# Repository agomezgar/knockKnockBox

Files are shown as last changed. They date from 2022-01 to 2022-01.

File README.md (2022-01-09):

# Knockknockbox Español

Un rediseño (un homenaje, si lo prefieres) de la mítica #KnockKnockBox con la que hemos jugado en tantos centros educativos gracias a los talleres Verkstadt de David Cuartielles
<p align="center">
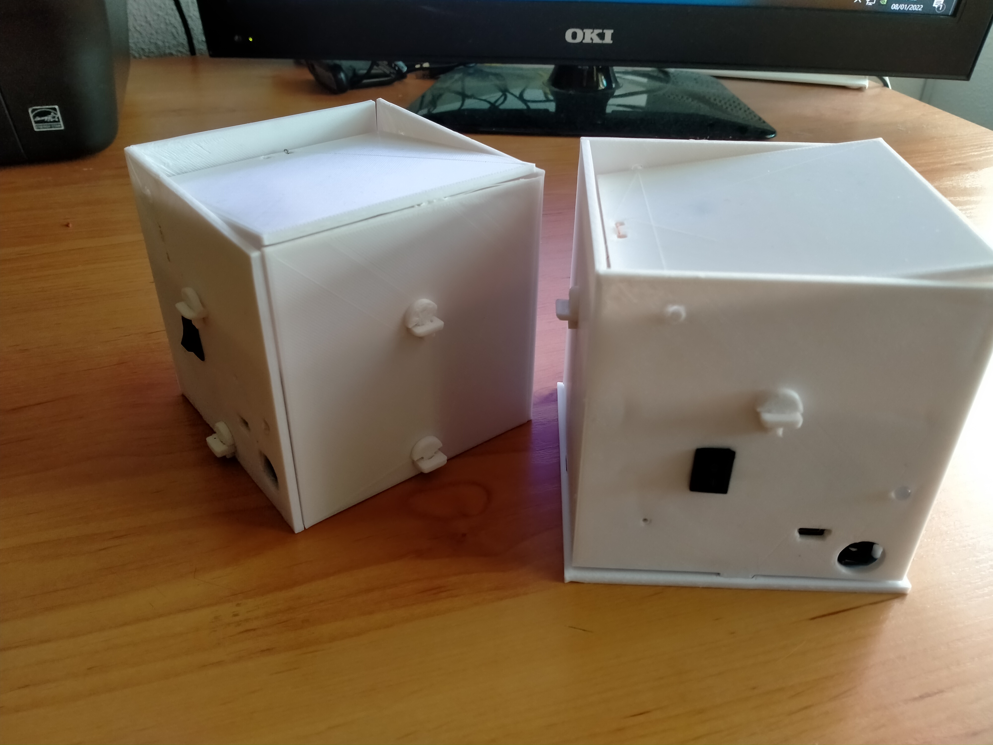
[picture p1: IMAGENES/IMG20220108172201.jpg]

</p>

## English

A redesign of the mytic #KnockKnockBox of the Verstakdt project by David Cuartielles

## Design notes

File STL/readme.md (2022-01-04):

## Español

Archivos en STL para imprimir en 3D

## English

STL files for 3D printing

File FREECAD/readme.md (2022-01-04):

## Español

Archivos CAD para su modificación por parte del aficionado que así lo desee

## English

CAD files at your disposal to modify them, if you wish

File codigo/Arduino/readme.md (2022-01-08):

## Español

Códigos de ejemplo para usar mediante la IDE de Arduino

## English

Example codes to be used with the Arduino's IDE

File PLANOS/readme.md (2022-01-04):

## Español

Planos de acuerdo a normativa ISO para la fabricación de cada pieza en madera

## English

Iso planes concerning the wood mechanization

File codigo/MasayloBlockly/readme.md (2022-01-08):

## ESPAÑOL

Códigos de ejemplo de uso de la Knockknockbox para programar con el IDE MasayloBlockly

##ENGLISH

Knockknockbox's use example codes to use to be programmed with MasayloBlockly

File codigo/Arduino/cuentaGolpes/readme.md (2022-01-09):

## Español

Golpea la caja cinco  veces en menos de dos segundos y se abrirá durante un segundo.

## English

Hit the box until 5 times in less than 2 seconds, and Knockknockbox will open. A second later, it will close again.

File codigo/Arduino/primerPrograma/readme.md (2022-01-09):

## Español

Primer programa para ayudar al aficionado a comprender el funcionamiento de la Knockknockbox

## English

First program to help amateurs to understand how Knockknockbox works.

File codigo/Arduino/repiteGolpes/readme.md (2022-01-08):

## Español

Golpea la caja hasta 30 veces. Después de una pausa de 2 segundos, la Knockknockbox reproducirá dicha secuencia con sonidos y luz.

##English

Hit the box until 30 times. After a 2 secs delay, the Knockknockbox will reproduce this sequence with both sound and light

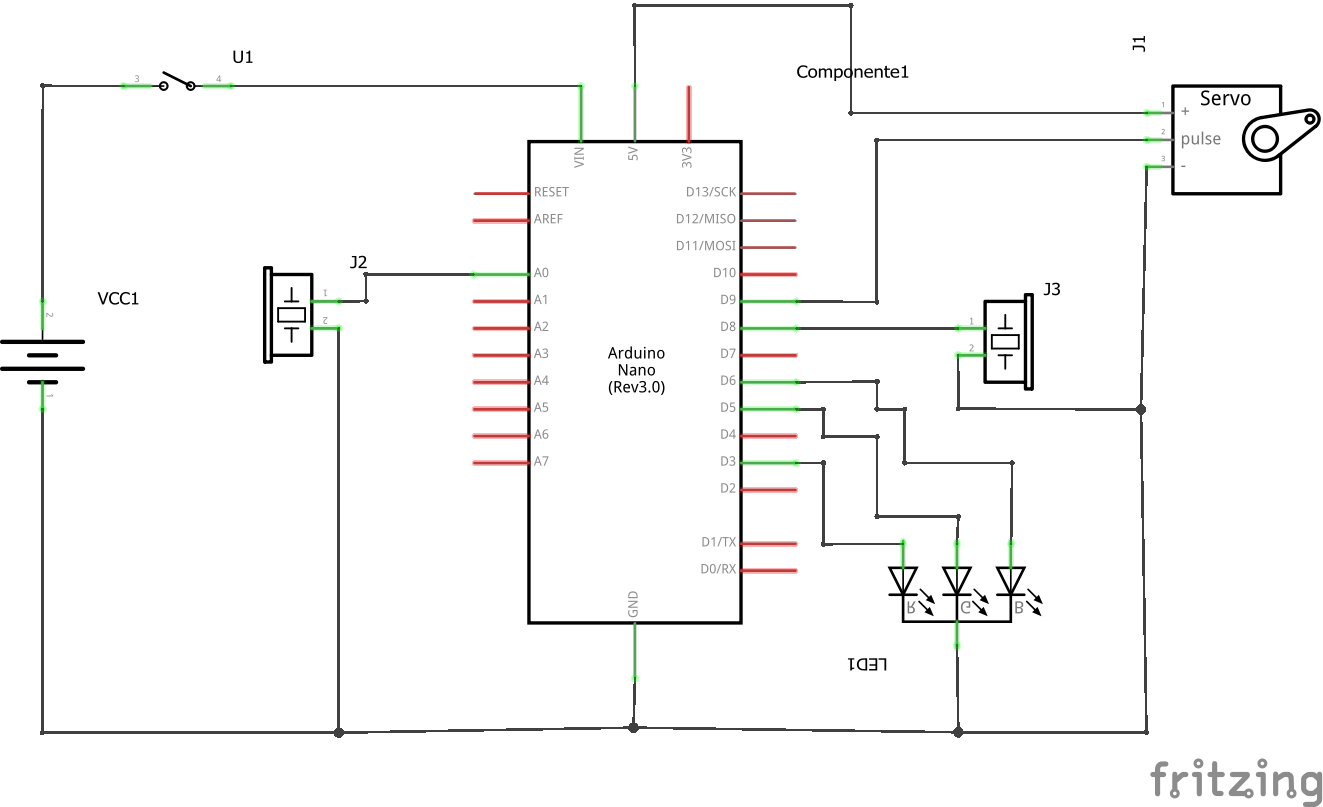
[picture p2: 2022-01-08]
PINOUT/esquemaConexionado.png

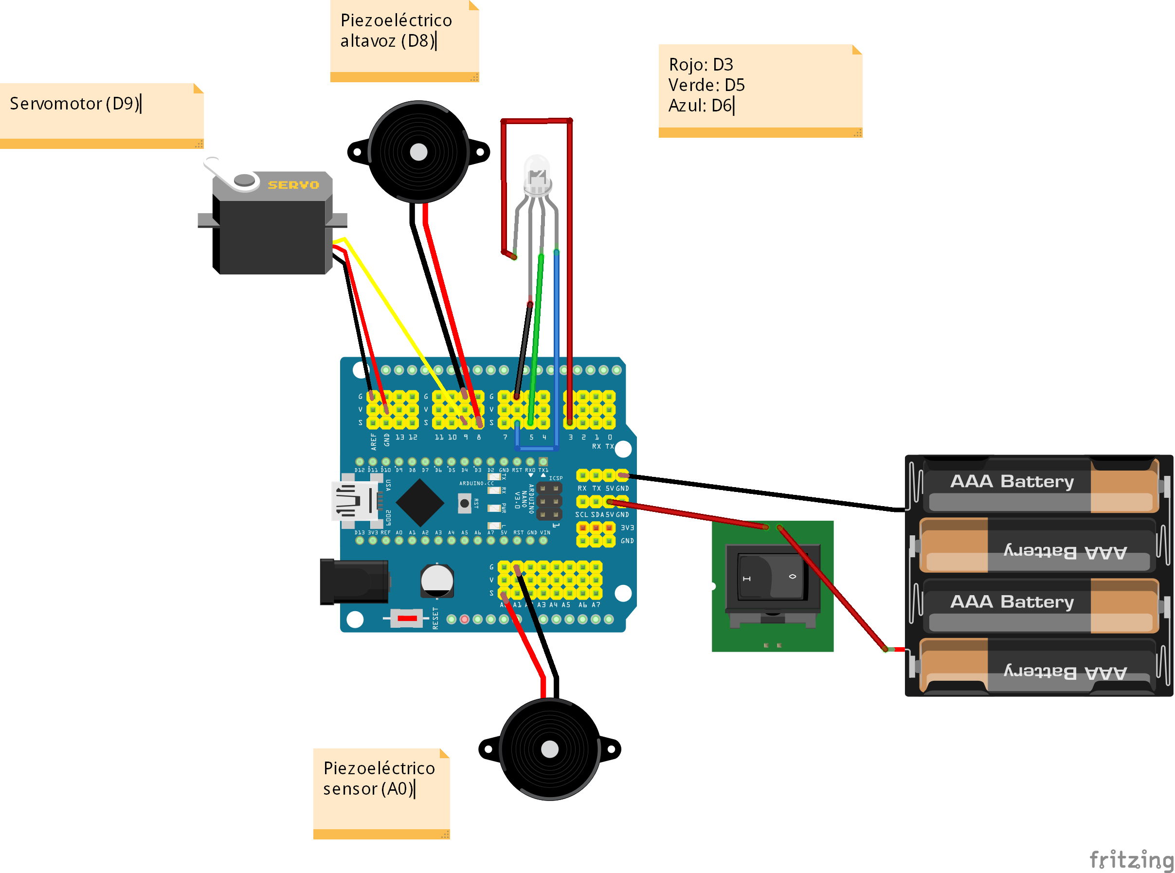
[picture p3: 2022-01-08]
PINOUT/esquemaConexion_bb.png

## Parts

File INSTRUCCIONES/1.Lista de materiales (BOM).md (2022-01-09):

# Lista de materiales

*Impresos en 3D*

| Pieza | Imagen |
| --- | --- |
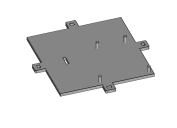
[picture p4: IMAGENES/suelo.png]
| Suelo |  |
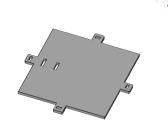
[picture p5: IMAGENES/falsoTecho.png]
| Doble fondo |  |
| Paredes frontal y trasera (tendrás que imprimir dos veces) |  |
| Pared lateral derecha, o pared lateral activa (llamada así porque aloja el interruptor del portapilas) |  |
| Pared lateral izquierda, o pared lateral inerte (en contraposición a la denominación de activa) |  |
| Soporte del servomotor SG-90 |  |
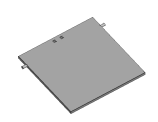
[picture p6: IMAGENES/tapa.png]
| Tapa |  |
| Pasador (pequeños fijadores). Tendrás que imprimir 8|  |

*Electrónica (vitaminas)

| Pieza | Imagen |
| --- | --- |
| Arduino UNO o Arduino Nano con su correspondiente shield. |  |
| Servomotor de posición SG-90 o similar|  |
| 2 piezoeléctricos pequeños (las piezas están equipadas para dos grandes o para dos pequeños). |  |
| (Alternativa) 2 piezoeléctricos grandes (las piezas están equipadas para dos grandes o para dos pequeños).|  |
| (Recomendable) 1 resistencia de 1 megaohmio o similar para proteger al piezo que hará de sensor de golpes. |  |
| 1 diodo RGB de 5 mm (uno normal también vale, pero te dará menos juego, claro). |  |

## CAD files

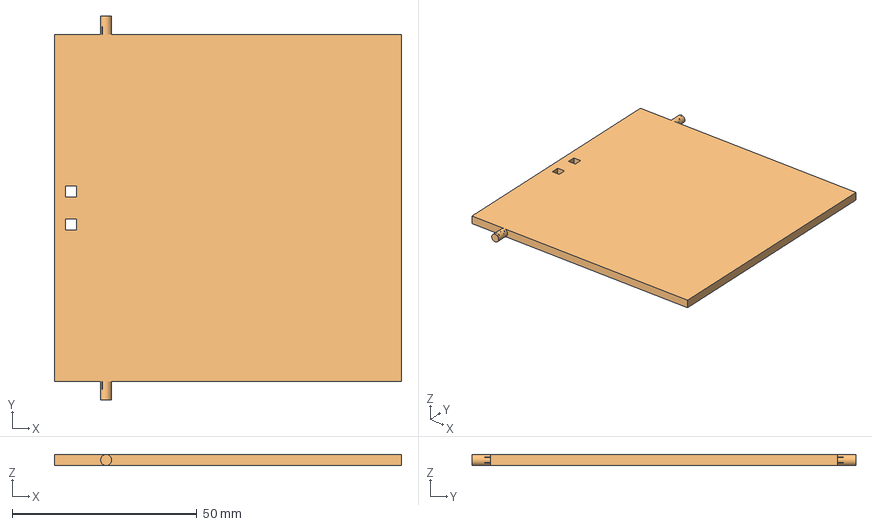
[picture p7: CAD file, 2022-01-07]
FREECAD/TAPA.FCStd
94.0 x 104.0 x 3.00 mm
tapa
tapa001
tapa (Meshed)

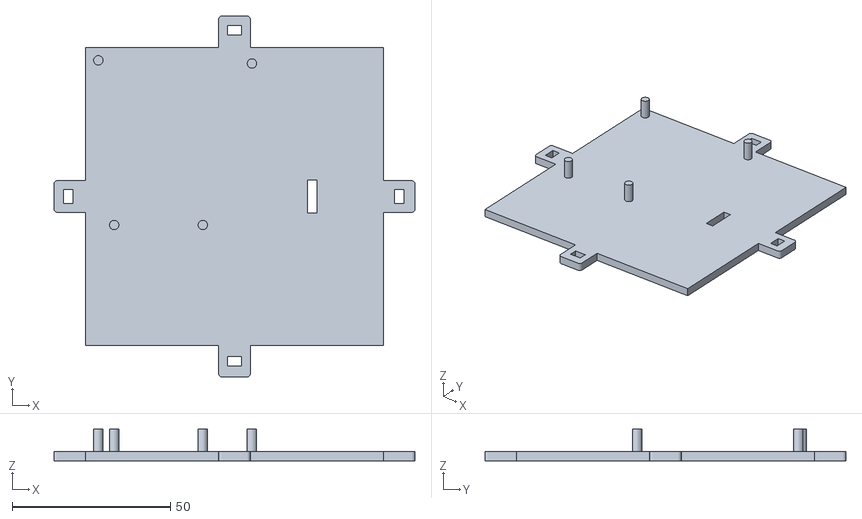
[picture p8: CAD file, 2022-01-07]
STL/sueloCaja.stl
114.0 x 114.0 x 10.0

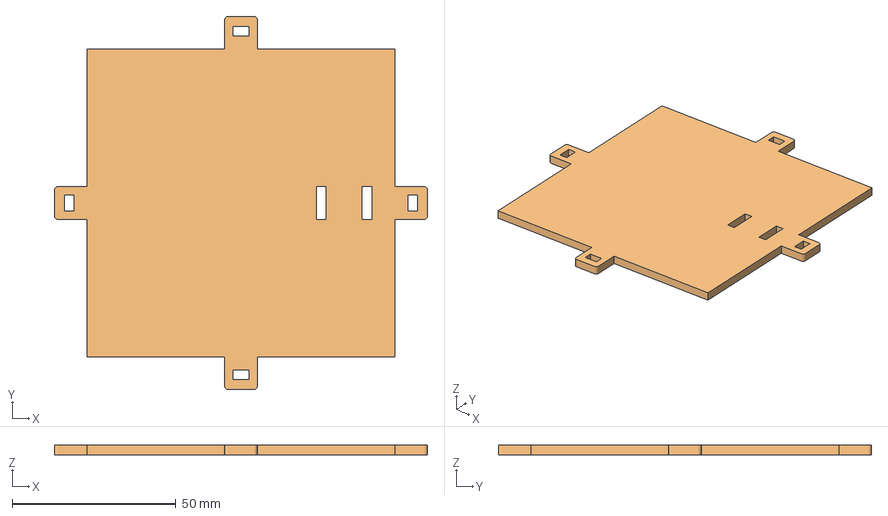
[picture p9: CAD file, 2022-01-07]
FREECAD/dobleFondo.FCStd
114.0 x 114.0 x 3.00 mm
falsoTecho
falsoTecho (Solid)
falsoTecho (Solid) (Meshed)

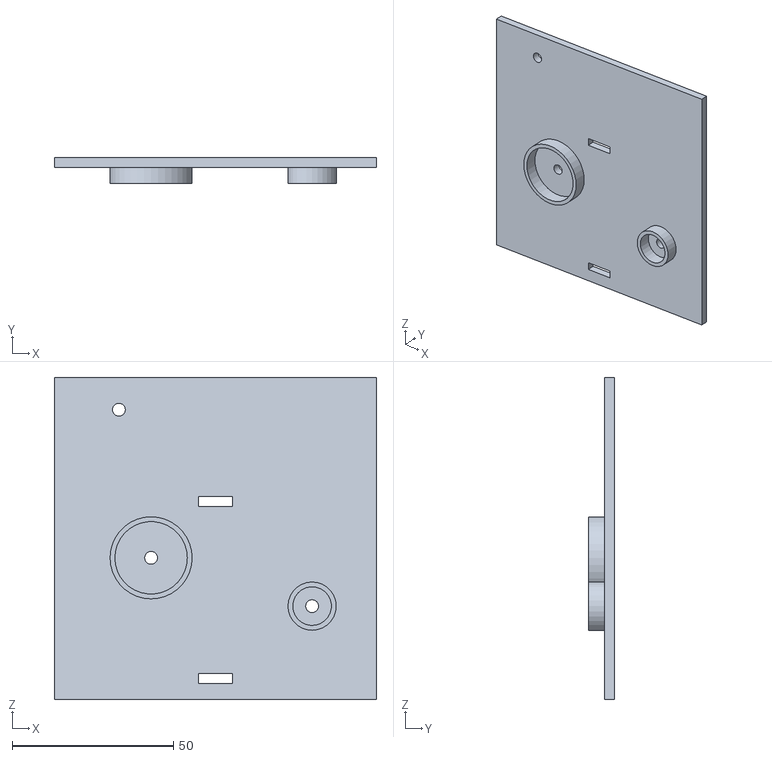
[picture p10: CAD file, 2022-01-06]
STL/lateralInerte.stl
100.0 x 8.00 x 100.0

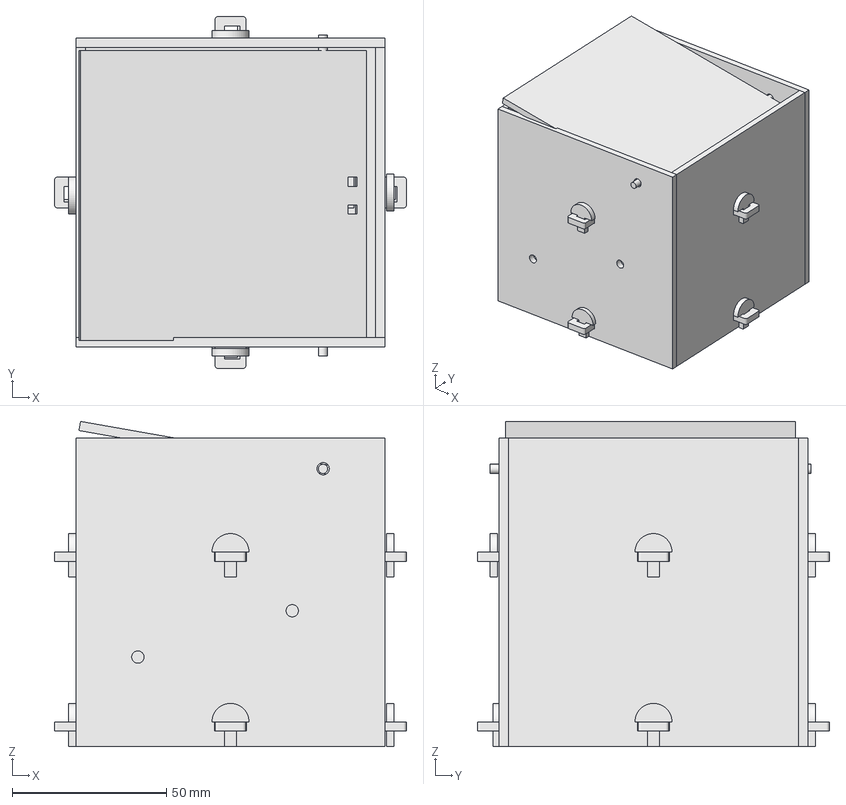
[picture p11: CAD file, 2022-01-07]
FREECAD/montajeGeneral.FCStd
114.0 x 114.0 x 105.3 mm
Cubo005
frontalTrasera (Solid)
frontalTrasera (Solid)001
lateralActiva001 (Solid)
tapa001
pasador002
pasador003
pasador004
pasador005
pasador006
pasador007
pasador008
pasador009
paredLateralInerte001
sueloCaja001
falsoTecho (Solid)
nano_expansion_shield(1)
Arduino_NANO

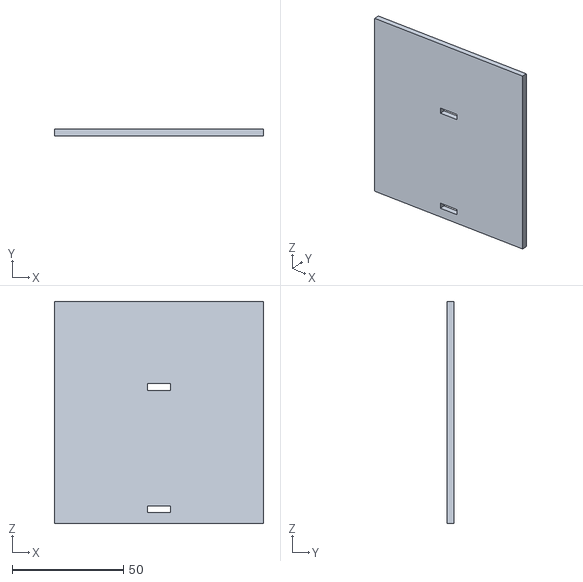
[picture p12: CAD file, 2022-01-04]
STL/frontalTrasera.stl
94.0 x 3.00 x 100.0

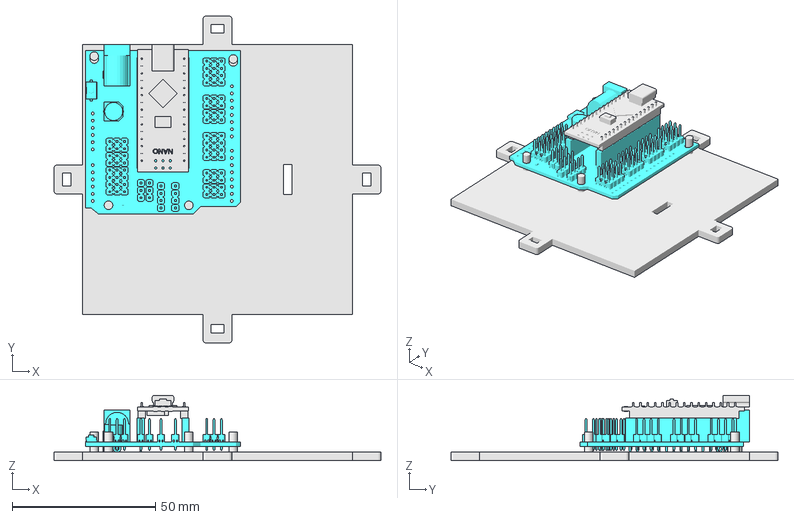
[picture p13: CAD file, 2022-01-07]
FREECAD/suelo.FCStd
114.0 x 114.0 x 22.7 mm
sueloCaja
sueloCaja001
nano_expansion_shield(1)
Arduino_NANO

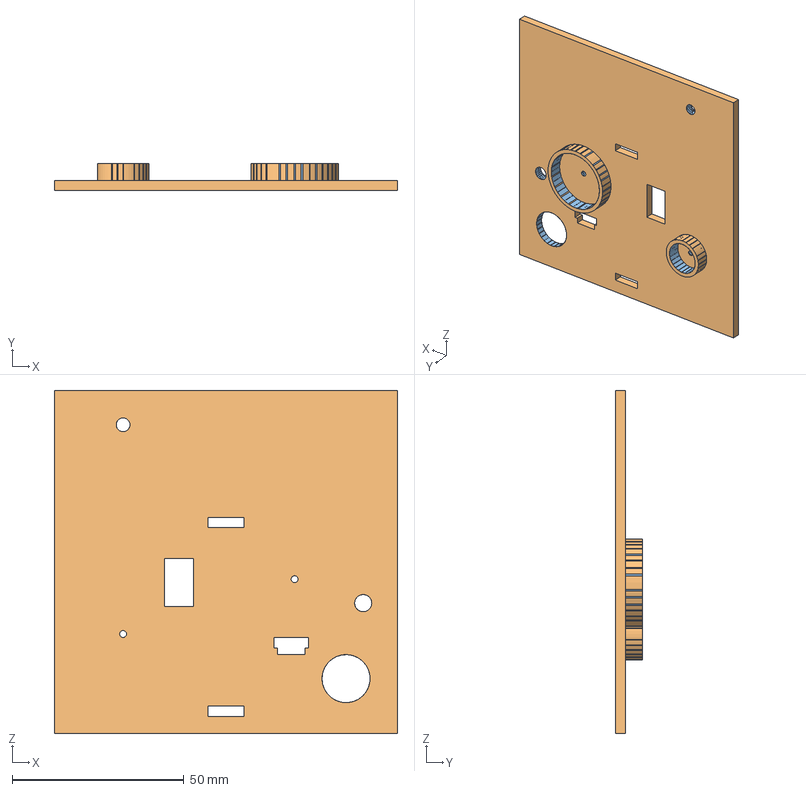
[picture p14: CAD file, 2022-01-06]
FREECAD/lateralActiva.FCStd
100.0 x 8.00 x 100.0 mm
lateralActiva001
lateralActiva001 (Solid)
lateralActiva001 (Solid) (Meshed)

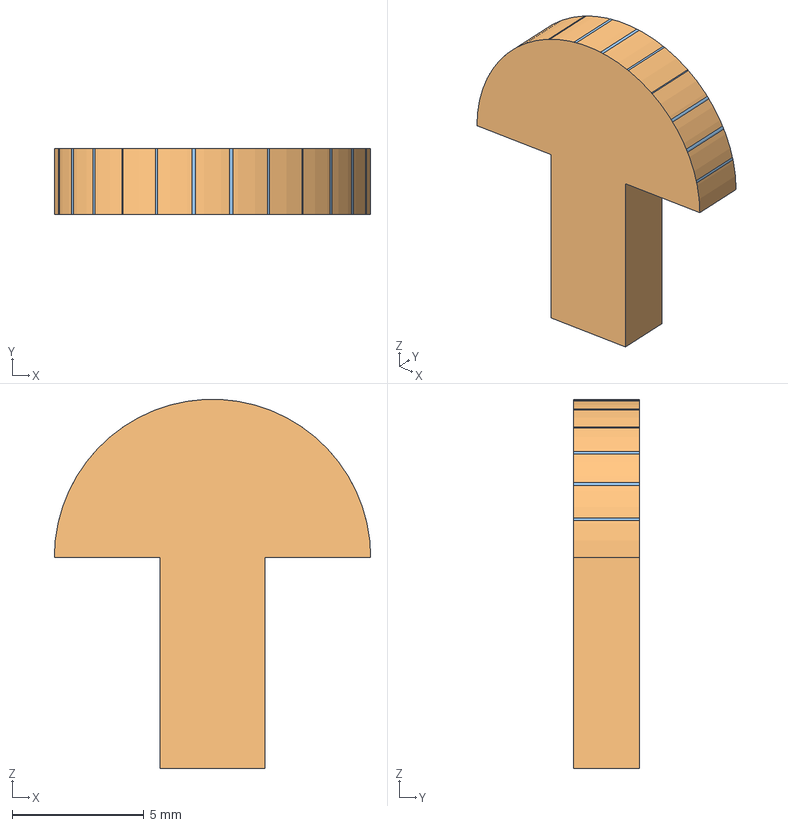
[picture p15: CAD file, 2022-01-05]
FREECAD/pasador.FCStd
12.0 x 2.50 x 14.0 mm
pasador
pasador002
pasador001

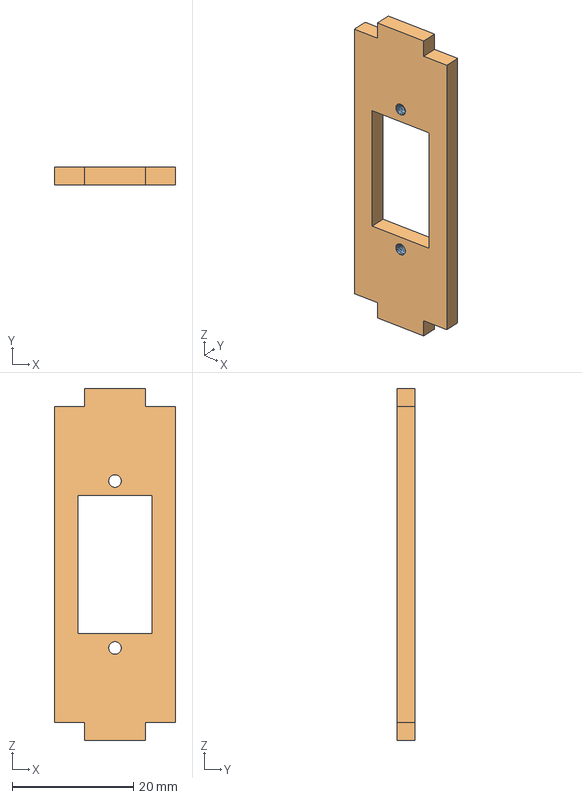
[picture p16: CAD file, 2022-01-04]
FREECAD/soporteServo.FCStd
20.0 x 3.00 x 58.0 mm
soporteServo
soporteServo (Meshed)

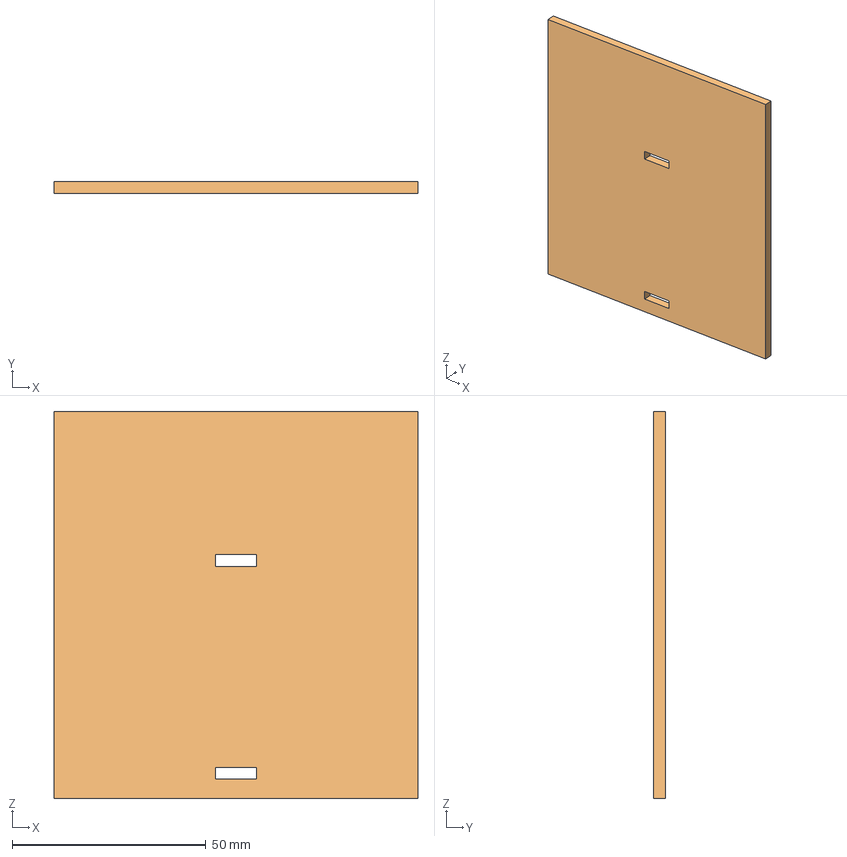
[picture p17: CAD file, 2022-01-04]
FREECAD/frontalyTrasera.FCStd
94.0 x 3.00 x 100.0 mm
frontalTrasera
frontalTrasera (Solid)
frontalTrasera (Meshed)

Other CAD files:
FREECAD/paredLateralInerte.FCStd
STL/dobleFondo.stl
STL/lateralActiva.stl
STL/pasador.stl
STL/soporteServo.stl
STL/tapa.stl

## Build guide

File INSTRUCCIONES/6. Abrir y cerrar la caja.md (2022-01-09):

# Abrir y cerrar la caja

Con este último ejemplo acabaría la introducción a la Knockknockbox. De hecho, es incluso más sencillo que el ejemplo anterior. Consiste en contar, digamos, cinco golpes, y al acabar el quinto golpe la caja se abre durante un segundo (la ponemos, por ejemplo, a 90 º) para a continuación volver a cerrarse. Para darle algo de salsa al código, impondremos la condición de que esos cinco golpes tienen que darse antes de cos segundos (2000 ms). Para ello, volveremos a usar la variable *contador* y además añadiremos otra variable de tipo **long** a la que llamaremos **tiempoActual** que continuamente se comparará con un comando básico de Arduino llamado **millis()** que devuelve los milisegundos transcurridos desde que el sistema se activa. Además, activaremos momentáneamente uno de los colores (digamos, por ejemplo, el verde) con cada golpe.

  <p align="center">
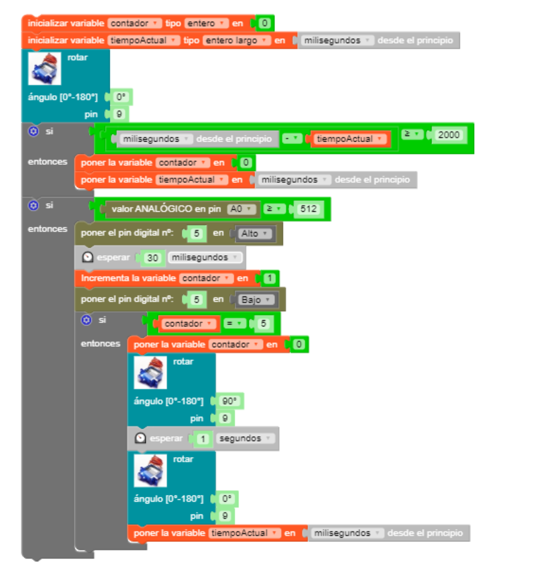
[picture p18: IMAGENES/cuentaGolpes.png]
  
    </p>
    
De nuevo os he dejado en la carpeta [codigo](../codigo/) el programa, tanto en su formato para MasayloBlockly como para la IDE de Arduino. De nada.

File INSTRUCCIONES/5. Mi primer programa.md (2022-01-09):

# Mi primer programa

Voy a dejarte sólamente un ejemplo que te permitirá familiarizarte con la Knockknockbox y sus posibilidades. Dicho programa tiene la siguientes características:

- Inicializa una variable de tipo entero llamada *contador* que empieza partiendo de 0. 
- El sensor de vibración detecta cada vez que damos un golpe. Espera 30 milisegundos (puedes cambiar el tiempo de rebote) y llama a la función **contar**, que irá aumentando el valor de *contador* de uno en uno. Según el valor de *contador*, cada vez que llamemos a **contar** sucederá una cosa distinta:
    - *1* encenderá el color rojo (pin 3) durante 1 segundo.
    - *2* encenderá el color verde (pin 5) durante 1 segundo.
    - *3* encenderá el color azul (pin 6) durante 1 segundo.
    - *4* hará que el altavoz (pin 8) toque la nota *Do*
    - *5* provocará la nota *Re*
    - *6* tocará la nota *Mi* y pondrá la variable *contador* a 0 para reiniciar el bucle.

El programa principal es sencillo:

  <p align="center">
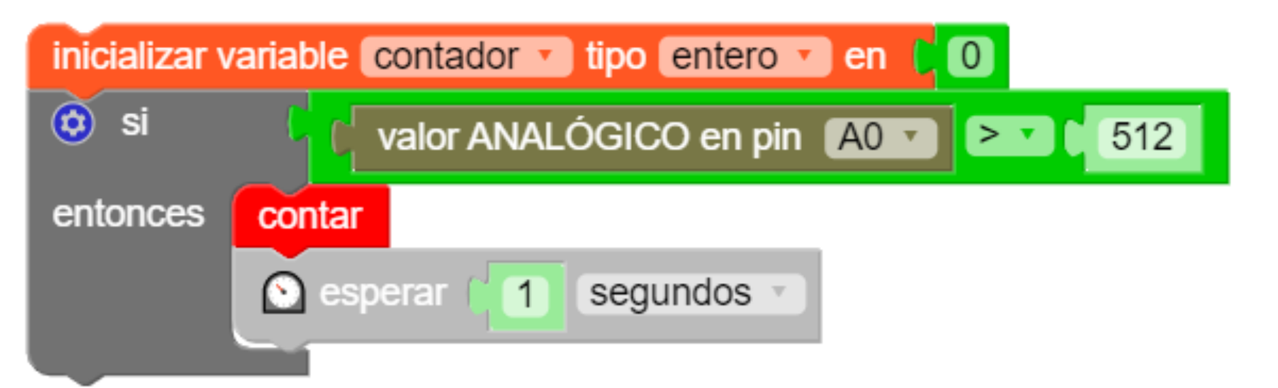
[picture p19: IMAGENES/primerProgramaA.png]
  
    </p>
    
En cuanto a la función **contar** (necesitaréis activar el bloque de opciones ***FUNCIONES*** de MasayloBlockly), si bien algo más larga (lo he hecho así para que resulte más sencillo de entender al neófito), tampoco es difícil de entender.

  <p align="center">
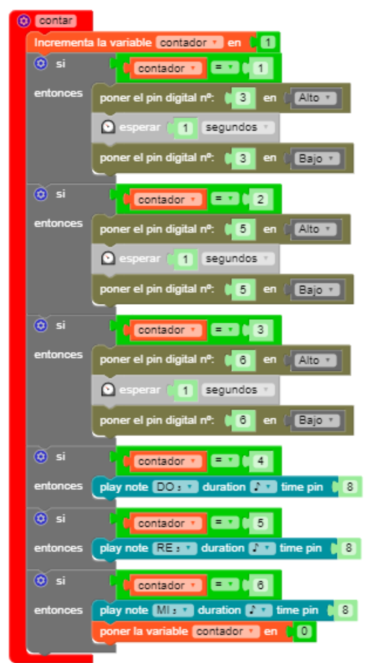
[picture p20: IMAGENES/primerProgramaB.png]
  
    </p>
    
¿A que mola?. Os he dejado en la carpeta [codigo](../codigo/) este primer programa para que lo probéis por vuestra cuenta.

***TRUQUI Podéis probar a graduar la intensidad de luz de cada color del diodo RGB mediante PWM (ya sabes, valores entre 0 y 255). Si encima activas dos o los tres colores combinando intensidades, podéis generar un montón de colores distintos.***

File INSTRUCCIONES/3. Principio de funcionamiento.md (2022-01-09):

# Principio de funcionamiento

Para jugar con la **Knockknockbox** sólo hay que golpearla. El sensor de vibraciones del dispositivo detectará las vibraciones, y de acuerdo a su programa, raaccionará abriendo o cerrando la caja, activando los colores del diodo RGB, o emitiendo sonidos a través del otro piezoeléctrico (***NOTA PARA FRIKIS: Sí, claro que podríamos utilizar un único piezoeléctrico para que realizara las dos funciones, pero eso implica un mayor grado de dificultad para el aficionado medio, además de que de momento su programación con el IDE MasayloBlockly no sería posible con esta configuración... ¡No seas tacaño y gasta dos buzzer!***

Puedes programar la Knockknockbox como te de la gana. Si respetas el pinout que te proporciono (y, si tienes algún conocimiento de Arduino,no tienes por qué), tendrás un piezoeléctrico como sensor de vibración en la patilla analógica A0, otro más como altavoz en el pin digital 8, y los colores rojo, verde y azul del RGB conectados a las salidas digitales 3, 5 y 6 (no sólo por capricho, que también, sino por poder utilizar la característica PWM de estos pines). El servo que abre la caja está conectado a la patilla 9.

<p align="center">
<image src="../PINOUT/esquemaConexionado.png" width="600">
</p>

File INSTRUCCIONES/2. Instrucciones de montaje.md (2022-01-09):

# Instrucciones de montaje

| Imagen | Descripción |
| --- | --- |
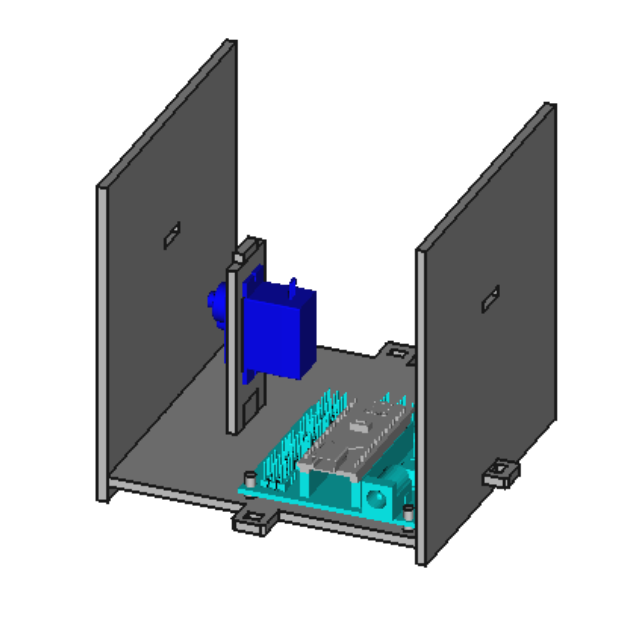
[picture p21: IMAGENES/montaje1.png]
|  | Inserta la Arduino en el suelo de la caja y atornilla el servomotor SG-90 a su soporte. A continuación, encaja dicho soporte en el suelo con el eje del servo apuntando a la pared trasera. Coloca las paredes frontal y trasera tal y como se ve en el dibujo. |
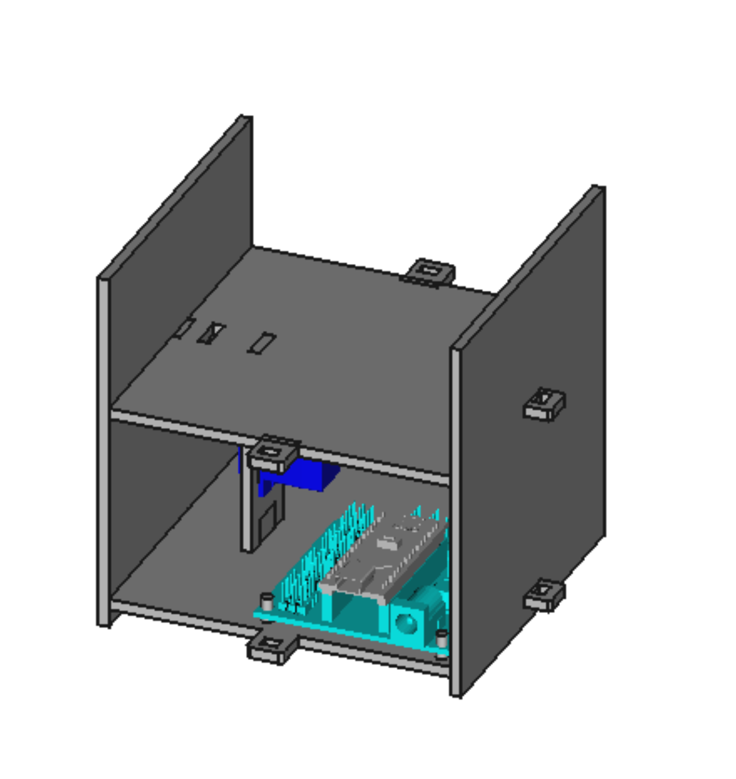
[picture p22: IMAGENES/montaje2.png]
|  | Encaja ahora la pieza que hemos llamado "doble fondo" tal y como se ve en la imagen. |
|  | Ha llegado el momento de realizar el conexionado. Encaja los dos piezos que tengas en la pared que quieras, coloca el interruptor y el LED en la pared lateral derecha y conecta de acuerdo a este esquema. |
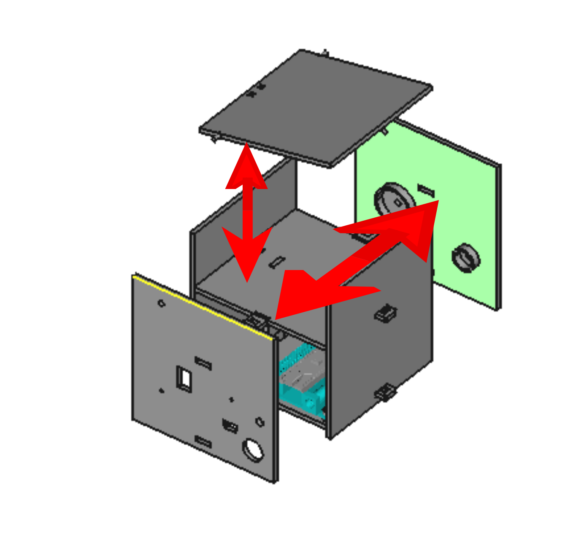
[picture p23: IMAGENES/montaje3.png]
|  | Vamos rematando. Ahora toca colocar las paredes laterales junto con la tapa. |
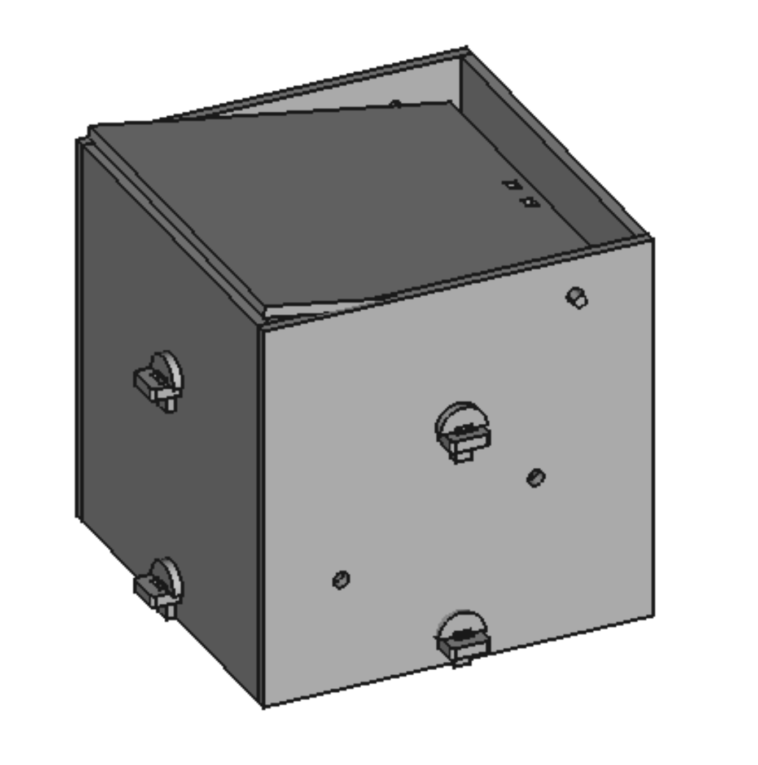
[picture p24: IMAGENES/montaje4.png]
|  | Pon los pasadores para fijar todas las paredes. Ya casi tienes la Knockknockbox. |
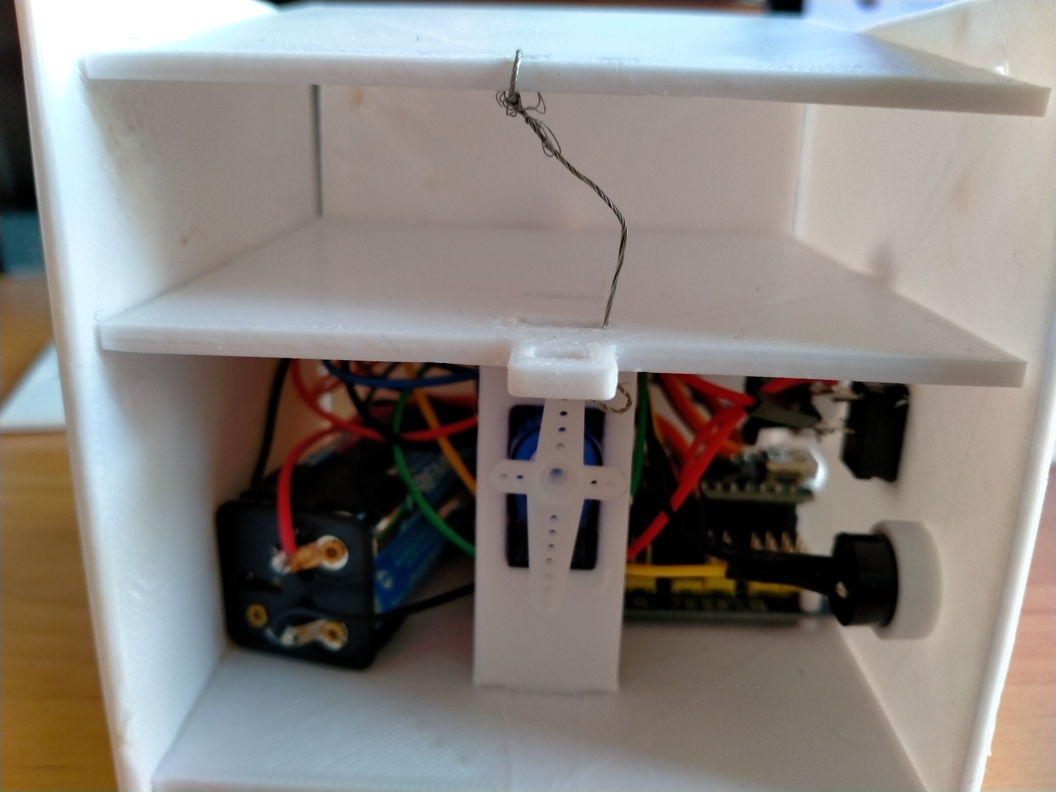
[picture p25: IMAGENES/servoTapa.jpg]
|  |Por último, quita un momento de nuevo la pared trasera y pon el servo a 0º (si no sabes cómo, puedes utilizar [el programa de calibración que tienes disponible aquí para MasayloBlockly](./codigo/MasayloBlockly/calibracionSensorVibracion/calibracionKnockknockbox.bloc) [y aquí para la IDE de Arduino](./codigo/Arduino/calibracionKnockknockbox/calibracionKnockknockbox.ino)) y coloca uno de los horns que vienen con el servo. Con un poco de hilo de cobre o náilon, ata un extremo de este "cuerno" a la tapa. Vuelve a cerrar la Knockknockbox con la pared que habías quitado. ¡Bueno!. ¡Pues ya estaría!  |

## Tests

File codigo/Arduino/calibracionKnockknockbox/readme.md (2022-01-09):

# Español

Usa este código para poner el servomotor a 0 º (tapa cerrada) y medir el valor de los golpes en el sensor de vibración a través del puerto serie.

# English

This code allows you to put your servo to 0 degrees (closed lid) and to measure the hit's value on the vibration sensor through the serial port.

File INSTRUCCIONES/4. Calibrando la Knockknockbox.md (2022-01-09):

 # Calibrando la Knockknockbox

Para jugar con la Knockknockbox sólo necesitas saber dos cosas: el umbral de detección de golpe (además del tiempo de rebote) y la posición ideal del servo para abrir la caja.

## Umbral de detección del golpe
  
¿Qué valor, entre 0 y 1023, debe detectar el pin analógico A0 de la Arduino para decidir si realmente se ha dado un golpe en la pared donde tenemos el sensor?. Esto puede depender mucho del tipo de piezoeléctrico que estéis usando. En mi caso, suelo utilizar un valor intermedio como 512, y desde ahí voy subiendo o bajando en diversas pruebas de ensayo y error.
  
De todos modos, en la carpeta [código](../codigo/) os he dejado un programa de calibración. En MasayloBlockly es así:
  <p align="center">
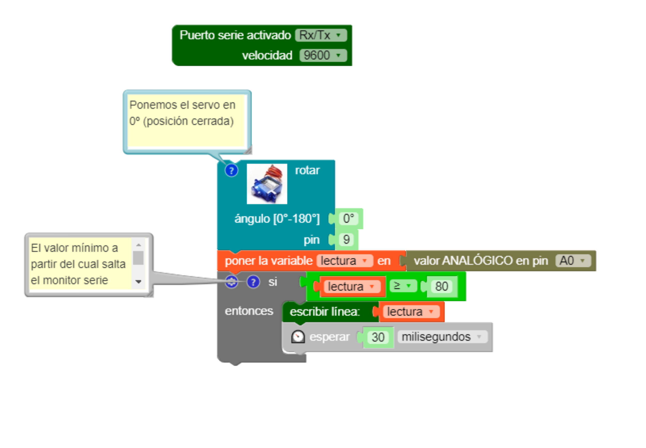
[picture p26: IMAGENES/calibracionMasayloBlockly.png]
  
    </p>
    
Dicho programa coloca en 0º el servomotor (correspondiente a tapa cerrada, de modo que puedas colocar el horn del servo tal y como te indicaba antes y lo ates a la tapa en tensión) y espera a obtener un valor mayor de 80 (umbral relativamente pequeño, pero puedes cambiarlo) para devolver por el puerto serie el valor medido. Aquí tienes un ejemplo de mi propia calibración:

  <p align="center">
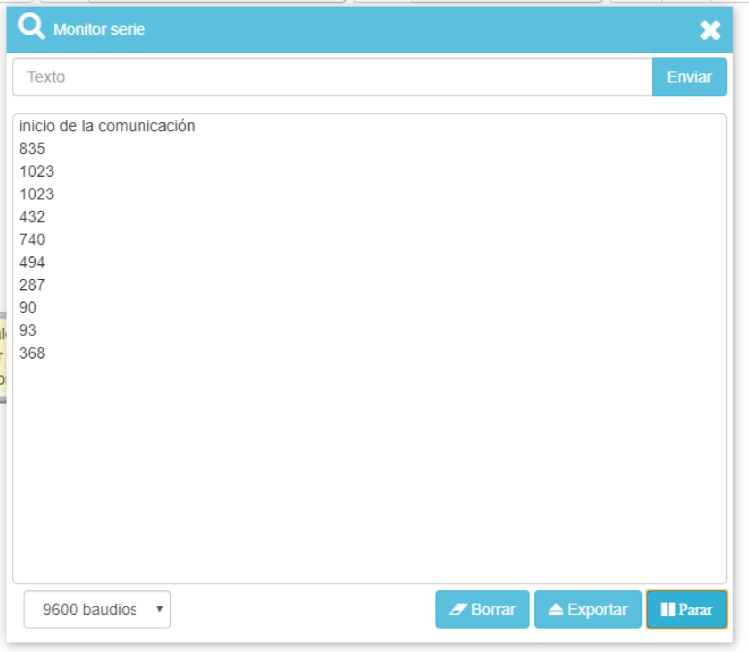
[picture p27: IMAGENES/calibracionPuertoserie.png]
  
    </p>
    
Como ves, en mi caso devuelve enseguida valores muy altos, así que para evitar falsas lecturas suelo utilizar umbrales del orden de 512 o mayores.

## Tiempo de rebote

Si has observado con atención el programa que te proponía antes, habrás notado que después de detectar un golpe, he establecido un pequeño retraso del orden de 30 milisegundos. Esto es debido porque poco después de recibir la vibración, el piezoeléctrico suele experimentar cierta realimentación, lo que hace que durante algunos milisegundos se siga enviando una falsa señal al pin analógico, lo que puede generar falsas lecturas. Por eso, *SIEMPRE* debes establecer un pequeño retraso (delay) justo después de que el programa decida que se ha recibido un golpe. Esto es lo que se conoce como *tiempo de rebote*. De nuevo, deberás decidir tú qué valor es el adecuado para que tu Knockknockbox no haga falsas lecturas. En mi caso, suelo trabajar entre 30 y 40 ms.

## Ángulo de apertura del servomotor

Este es quizás el aspecto que exige más cuidado de la calibración de la Knockknockbox. Ya sé que si pongo el servomotor a 0º, la tapa se mantendrá cerrada. Un valor que sé seguro que provocará la apertura de la caja es el máximo disponible, de 180 º que provocará que el horn de media vuelta y por lo tanto tire del hilo que provocará la apertura de la tapa. Ahora bien, dependiendo de la tensión con que haya atado el hilo, puedo encontrarme con que dicha posición genere una tensión excesiva que pueda provocar daños al servo, a la Knockknockbox o a ambos.

A este respecto, sólo puedo proponerte que vayas experimentando con diversos valores de apertura (por ejemplo, 45 º) y paulatinamente vayas decidiendo cuál puede ser la cifra adecuada. De nuevo, si usas MasayloBlockly lo tienes chupado:

  <p align="center">
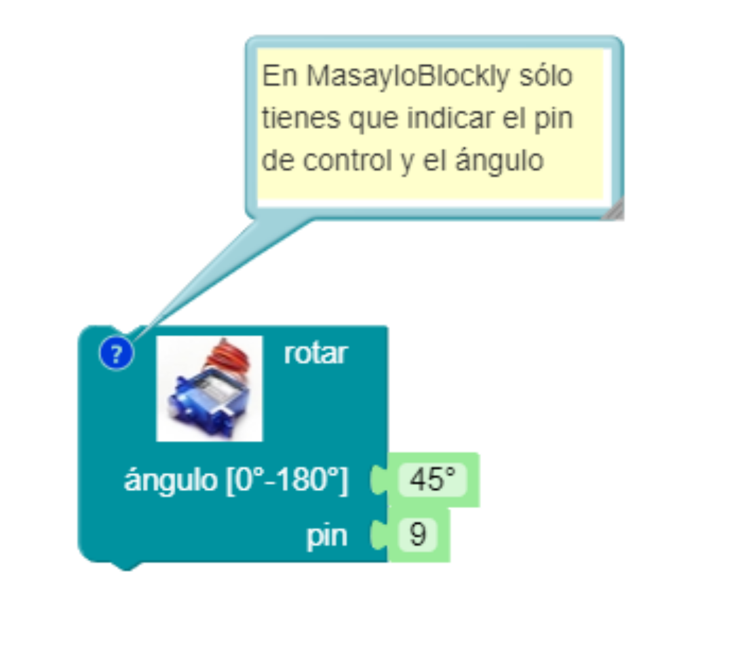
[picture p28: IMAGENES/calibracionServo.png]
  
    </p>

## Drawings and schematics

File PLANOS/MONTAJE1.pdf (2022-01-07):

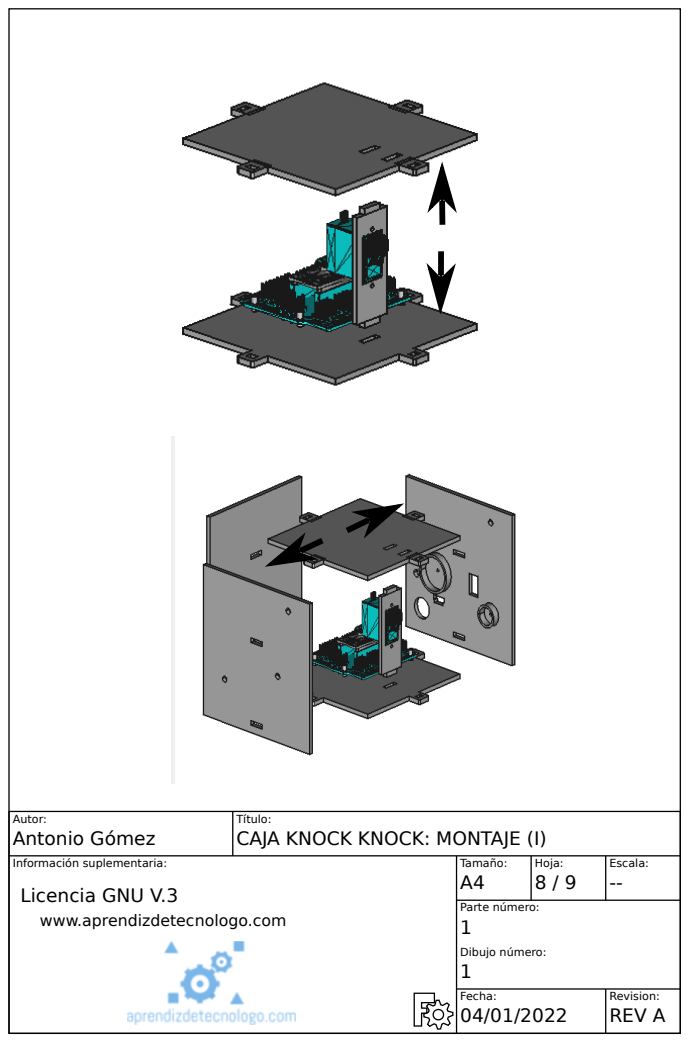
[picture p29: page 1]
Autor:; Título:; Información suplementaria:; Tamaño:; Hoja:; Escala:; Parte número:; Dibujo número:; Fecha:; Revision:; Antonio Gómez; CAJA KNOCK KNOCK: MONTAJE (I); Licencia GNU V.3; REV A

www.aprendizdetecnologo.com

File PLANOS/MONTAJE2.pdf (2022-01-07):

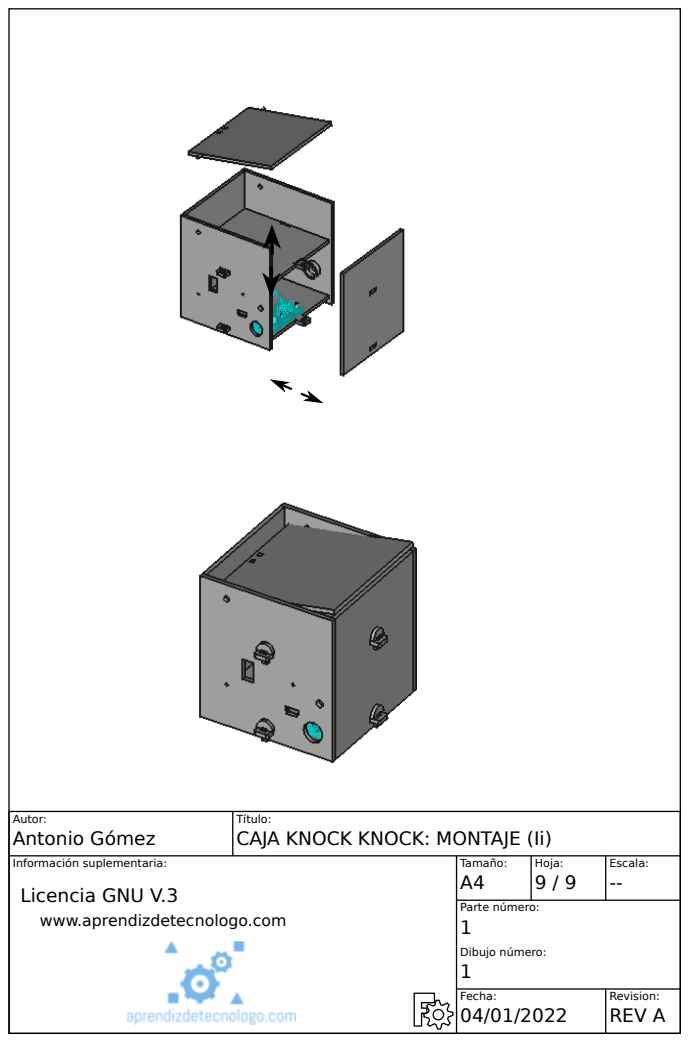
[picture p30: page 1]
Autor:; Título:; Información suplementaria:; Tamaño:; Hoja:; Escala:; Parte número:; Dibujo número:; Fecha:; Revision:; Antonio Gómez; CAJA KNOCK KNOCK: MONTAJE (Ii); Licencia GNU V.3; REV A

www.aprendizdetecnologo.com

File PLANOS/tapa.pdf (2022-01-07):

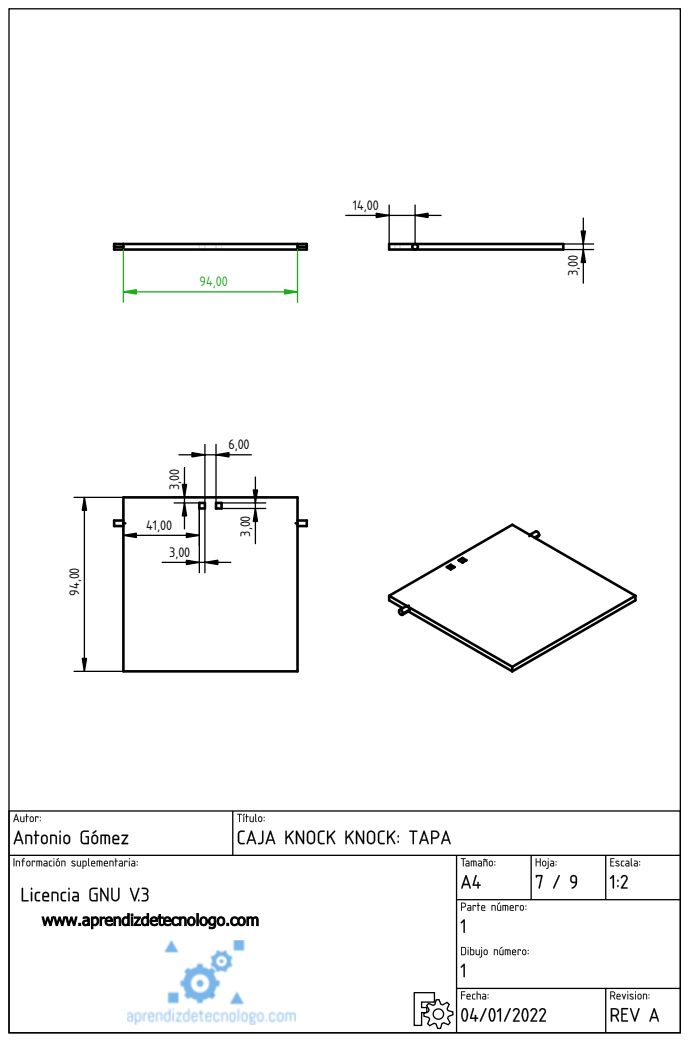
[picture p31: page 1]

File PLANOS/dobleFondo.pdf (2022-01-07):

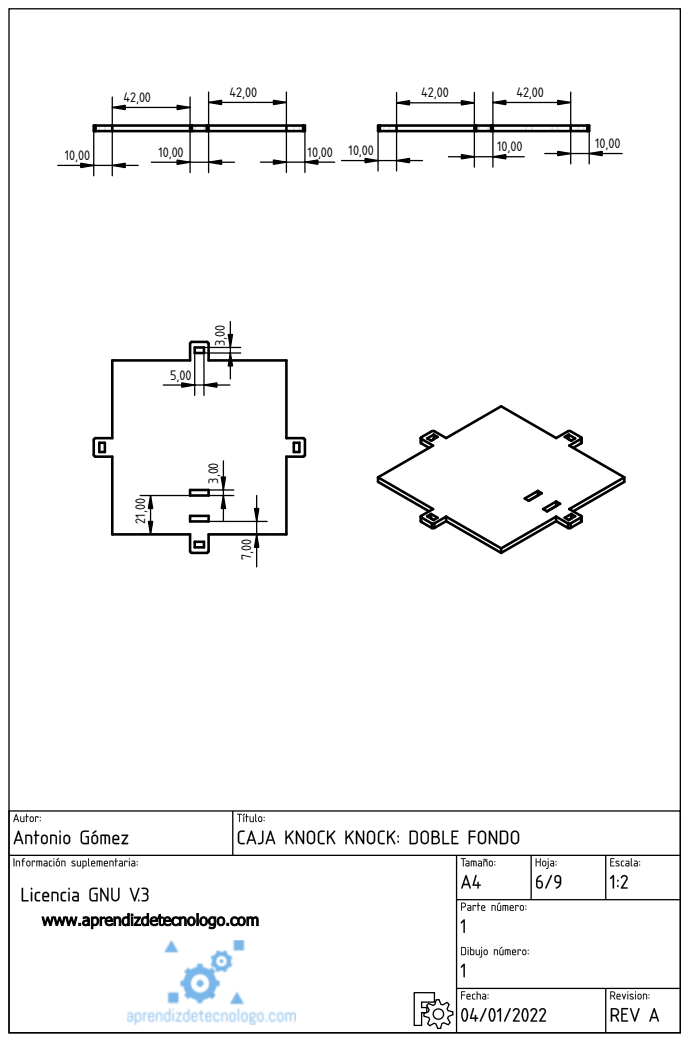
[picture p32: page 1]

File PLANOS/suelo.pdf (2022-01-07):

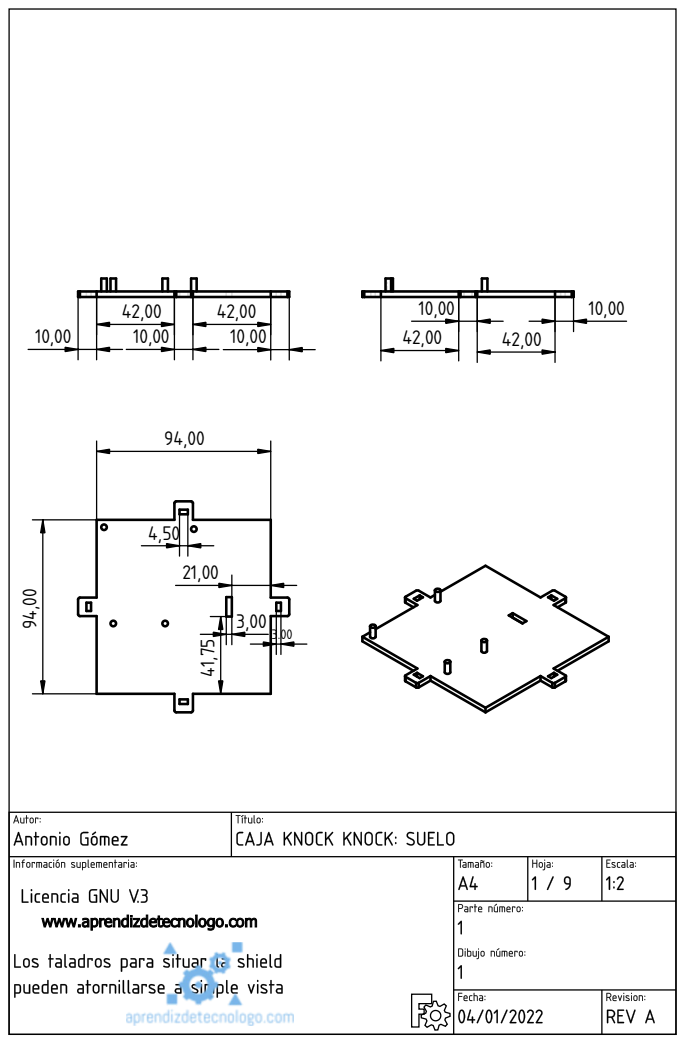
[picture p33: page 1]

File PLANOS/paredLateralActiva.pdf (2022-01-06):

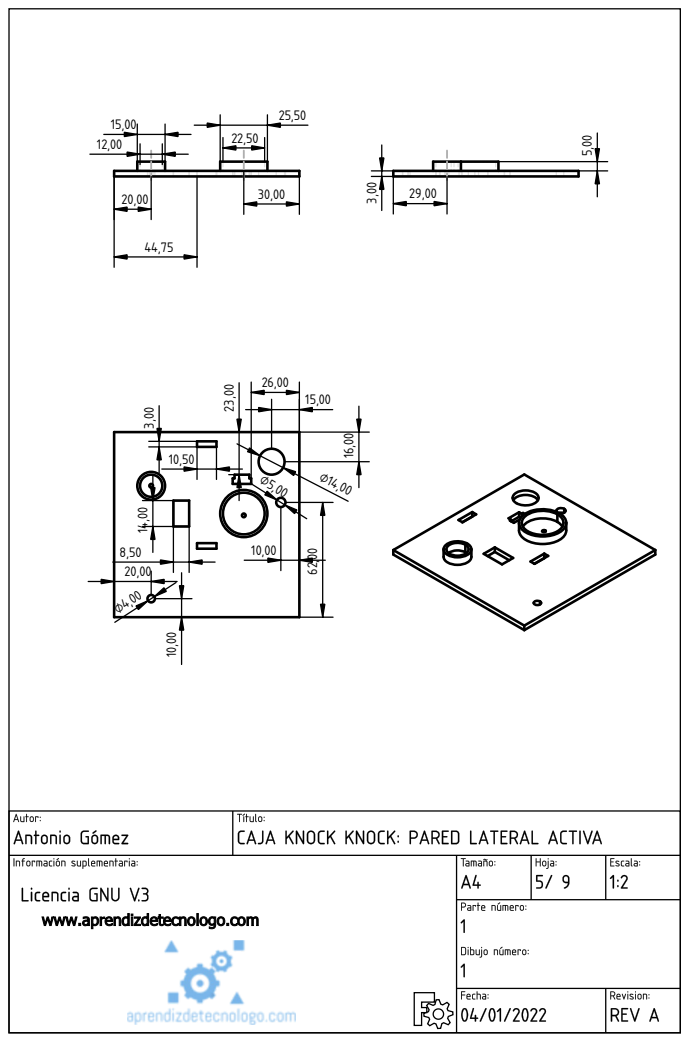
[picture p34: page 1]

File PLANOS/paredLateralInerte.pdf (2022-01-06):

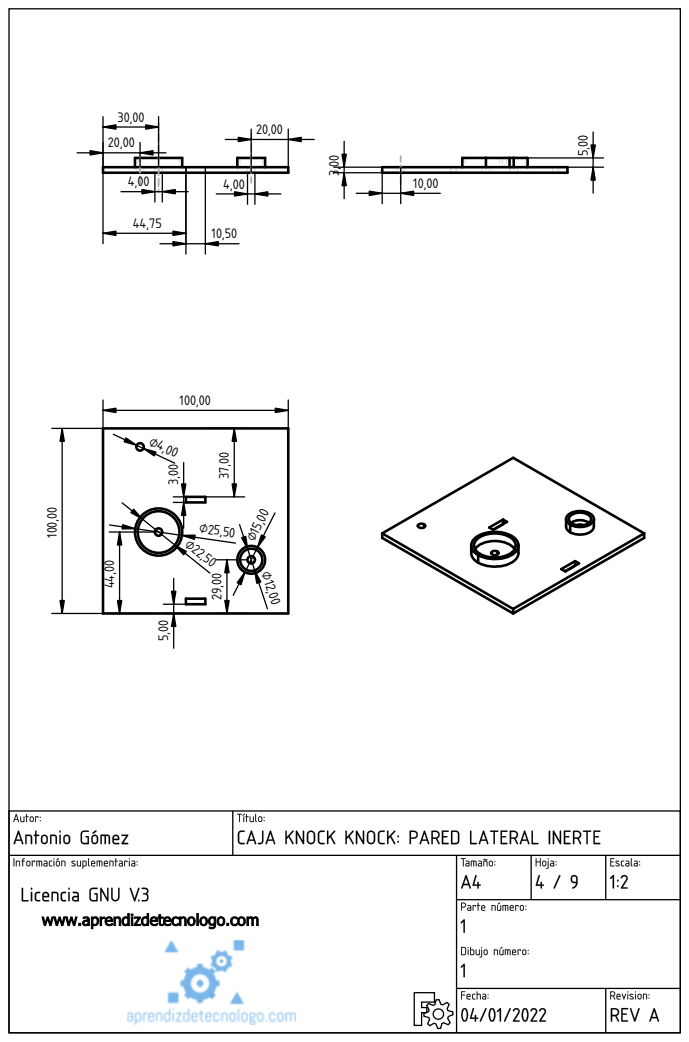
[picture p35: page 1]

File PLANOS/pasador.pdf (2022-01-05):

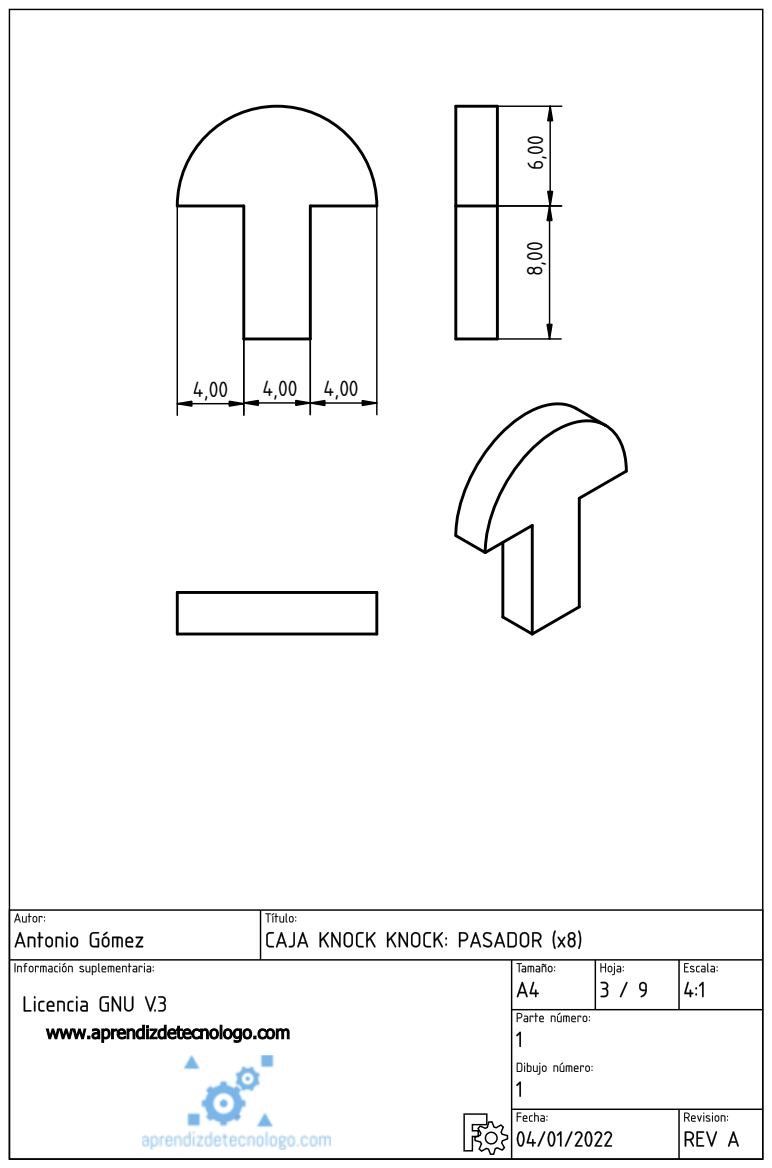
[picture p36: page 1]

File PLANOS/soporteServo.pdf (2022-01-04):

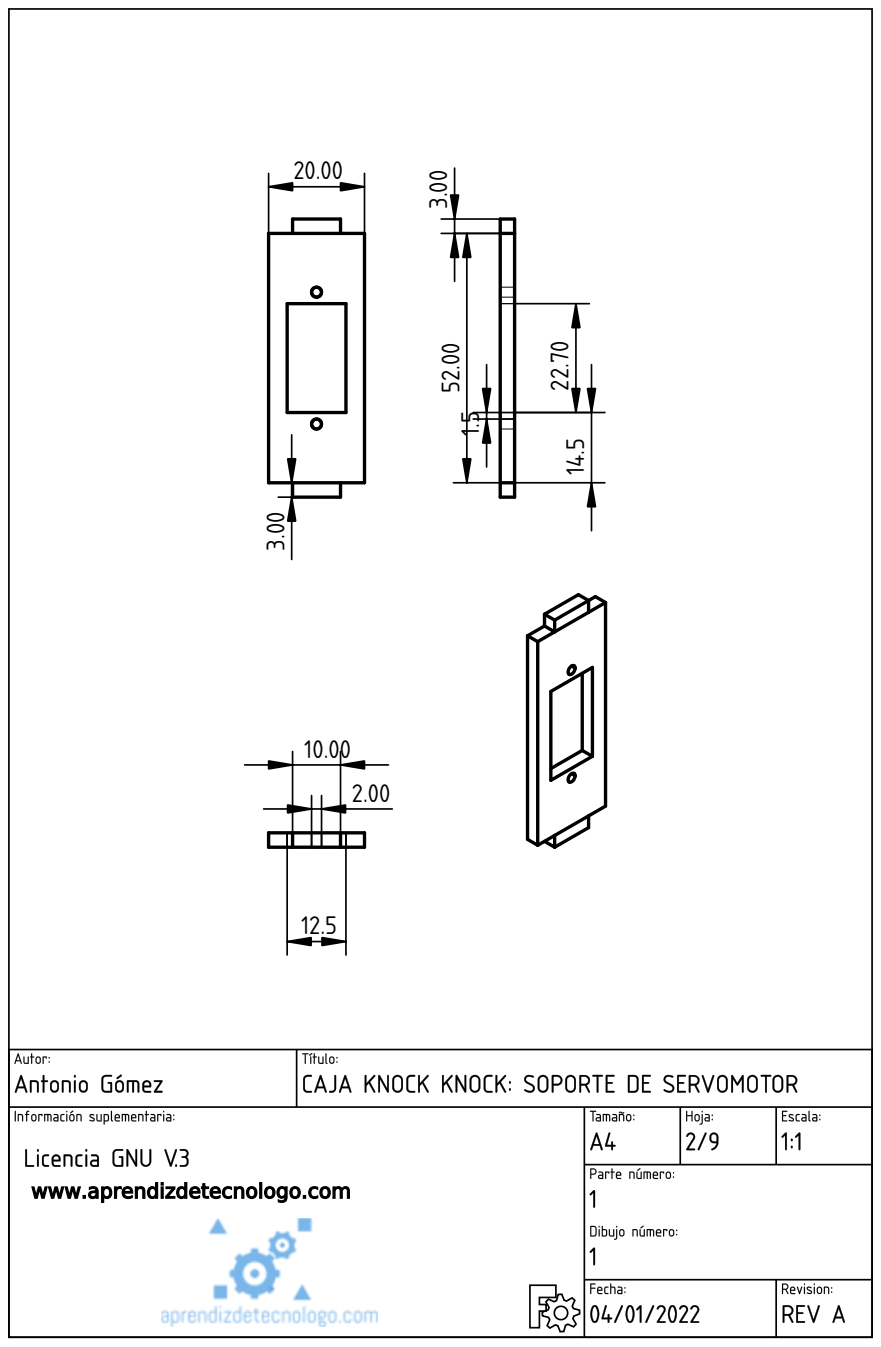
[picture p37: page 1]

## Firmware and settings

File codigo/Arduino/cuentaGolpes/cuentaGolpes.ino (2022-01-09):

/*
 uentaGolpes. Golpea la pared cinco veces en menos de dos segundos para abrir la caja. - Example code for the knockknockBox.
  Created by Antonio Gomez Garcia and Mª Dolores Nogueras Atance, january 8, 2022.
  Released into the public domain.
*/
#include <Servo.h>

int contador = 0;
long tiempoActual = millis();

Servo servo_9;

void setup() {
  servo_9.attach(9);
  pinMode(5, OUTPUT);
}

void loop() {
  servo_9.write(0);
  if (millis() - tiempoActual >= 2000) {
    contador = 0;
    tiempoActual = millis();
  }
  if (analogRead(A0) >= 512) {
    digitalWrite(5, HIGH);
    delay(30);
    contador = contador + 1;
    digitalWrite(5, LOW);
    if (contador == 5) {
      contador = 0;
      servo_9.write(90);
      delay(1*1000);
      servo_9.write(0);
      tiempoActual = millis();
    }
  }

}

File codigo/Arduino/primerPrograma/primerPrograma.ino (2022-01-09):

/*
 Primer programa - Example code for the knockknockBox.
  Created by Antonio Gomez Garcia and Mª Dolores Nogueras Atance, january 8, 2022.
  Released into the public domain.
*/
int contador = 0;

void contar() {
  contador = contador + 1;
  if (contador == 1) {
    digitalWrite(3, HIGH);
    delay(1*1000);
    digitalWrite(3, LOW);
  }
  if (contador == 2) {
    digitalWrite(5, HIGH);
    delay(1*1000);
    digitalWrite(5, LOW);
  }
  if (contador == 3) {
    digitalWrite(6, HIGH);
    delay(1*1000);
    digitalWrite(6, LOW);
  }
  if (contador == 4) {
    tone(8,261,250);
    delay(250);
  }
  if (contador == 5) {
    tone(8,293,250);
    delay(250);
  }
  if (contador == 6) {
    tone(8,329,250);
    delay(250);
    contador = 0;
  }
}

void setup() {
  pinMode(3, OUTPUT);
  pinMode(5, OUTPUT);
  pinMode(6, OUTPUT);
  pinMode(8, OUTPUT);
}

void loop() {
  if (analogRead(A0) > 512) {
    delay(0.1*1000);
    contar();
  }
}

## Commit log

2022-01-09 Create 1.Lista de materiales (BOM).md
2022-01-09 Update 1.Lista de materiales (BOM).md
2022-01-09 Create 2. Instrucciones de montaje.md
2022-01-09 Create 3. Principio de funcionamiento.md
2022-01-09 Create 4. Calibrando la Knockknockbox.md
2022-01-09 Create 6. Abrir y cerrar la caja.md
